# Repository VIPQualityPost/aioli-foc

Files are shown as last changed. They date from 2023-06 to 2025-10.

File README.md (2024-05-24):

# AIOLI-FOC (All In One Low I - FOC)

Small, low current (I) closed loop simpleFOC driver board, that can be assembled for &lt;$10 with mostly basic components at LCSC. Has USB C for power, serial communication (USB CDC), and DFU firmware updates. The CANBUS peripheral is exposed on both edges for "stitching" boards together using the Kyocera B2B connector used on the STLINK-V3-MINIE. SWD + UART via STLINK 14 pin connector.

The target for this project was to create an all-in-one simpleFOC board with high resolution magnetic encoder, better MCU than the previous STM32F103, CANBUS for multi board communication, and be assembled with top-side only components. The board is 4 layers (which at this size, does not add any cost over the 2-layers). Additionally, it has a compact size of 40x40mm.

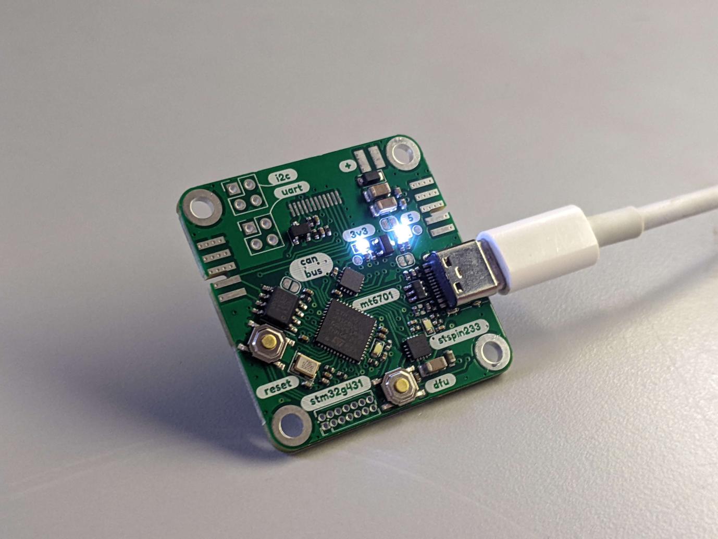
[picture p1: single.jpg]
Photo of PCB

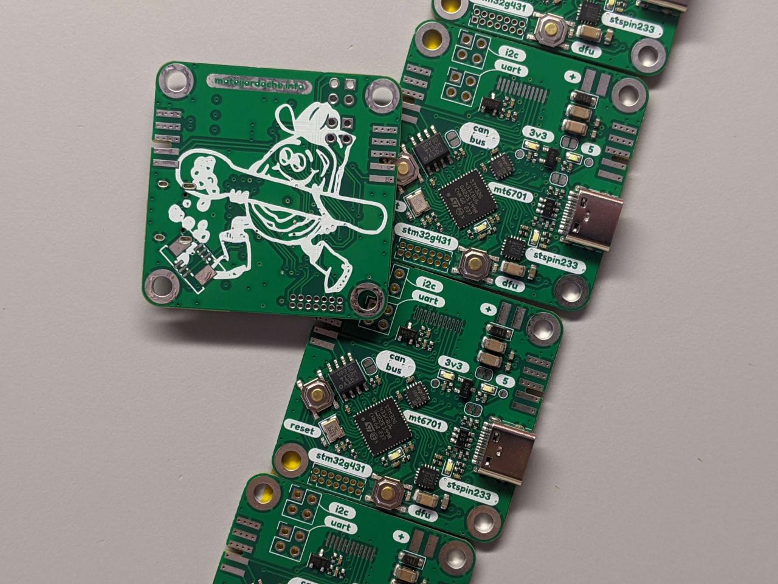
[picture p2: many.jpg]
Photo of PCBs


# Building

- Install [platformio core](https://docs.platformio.org/en/latest/core/installation/methods/index.html)
- Run `pio run`

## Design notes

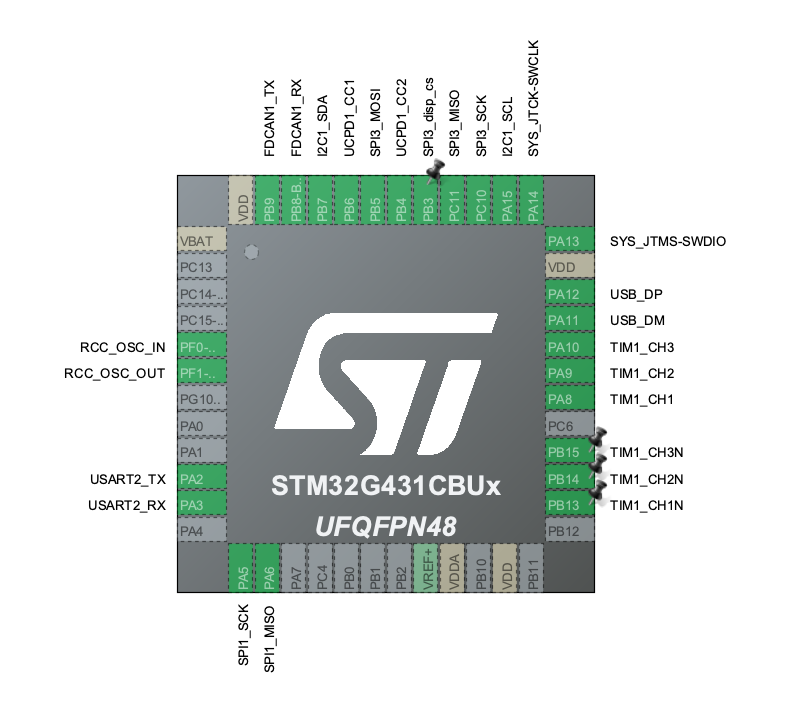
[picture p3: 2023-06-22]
stm32g431-pinout.png

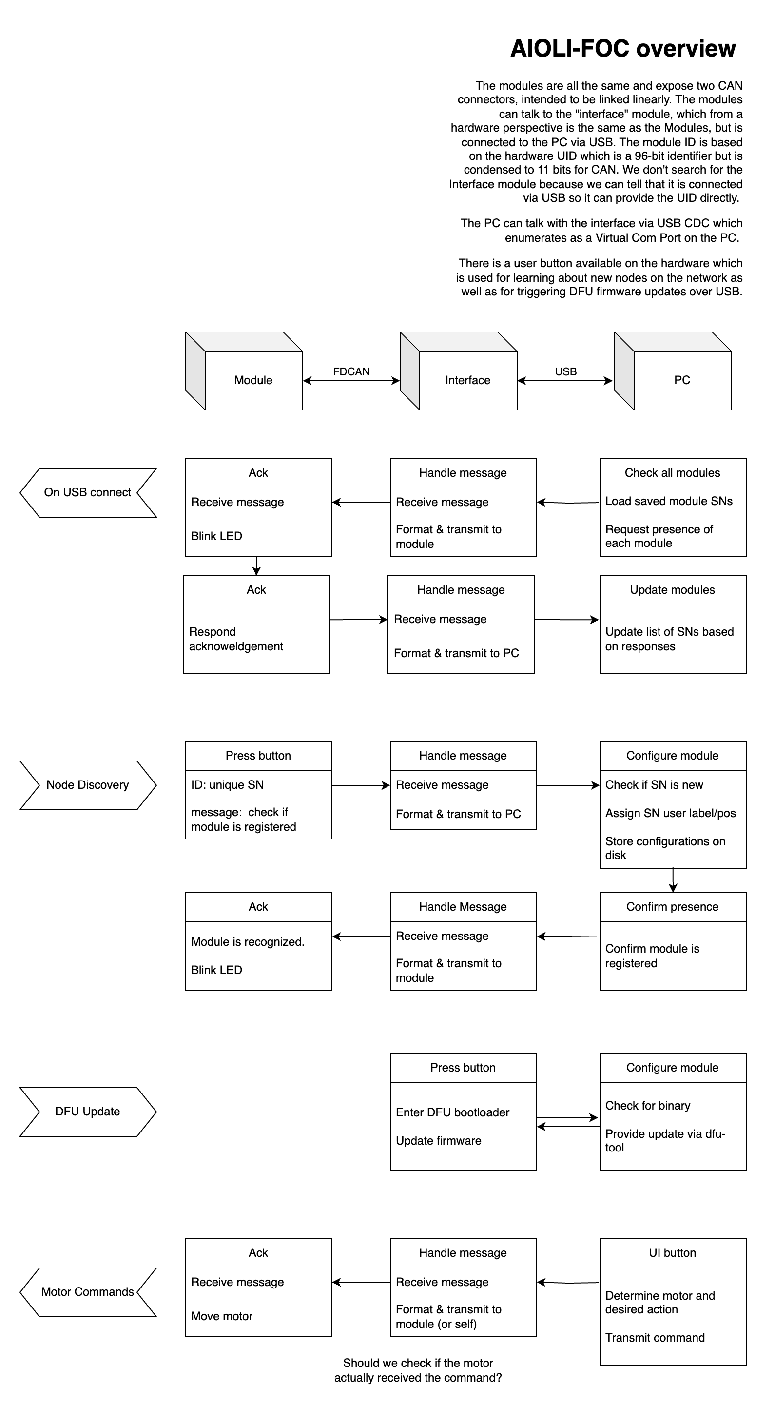
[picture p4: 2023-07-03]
aioli-foc-overview.png

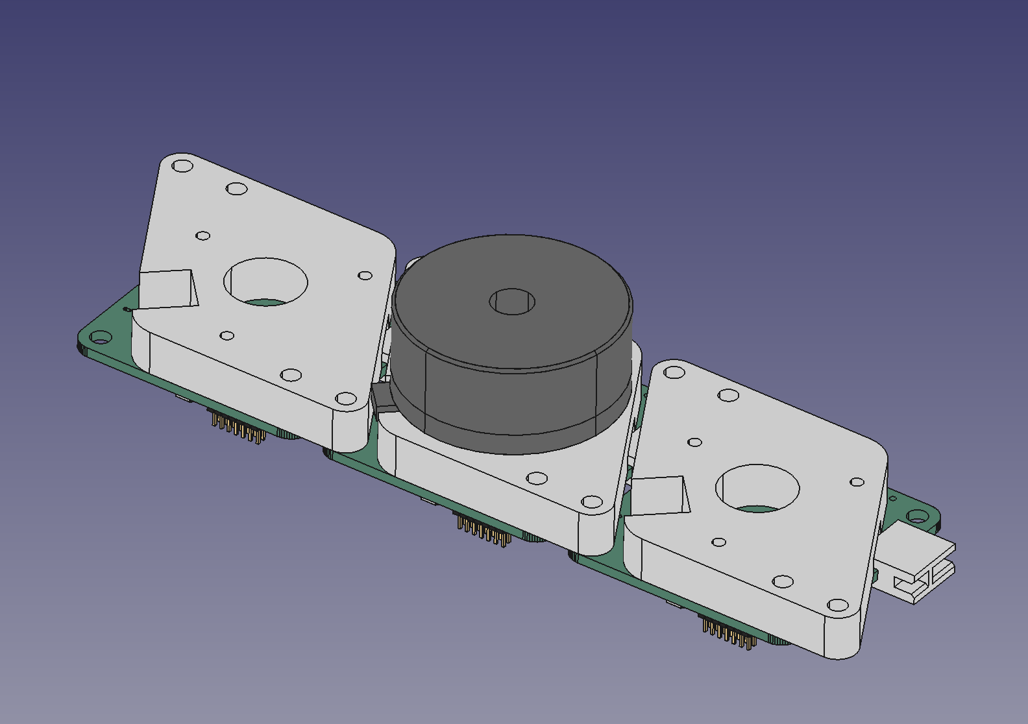
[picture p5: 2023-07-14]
mechanical/motor_MAD/render.png

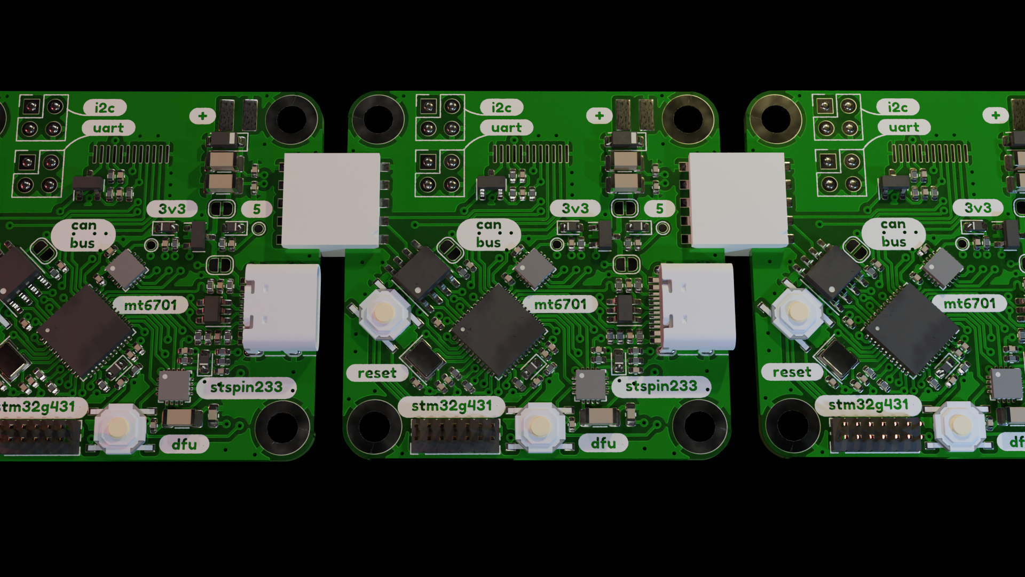
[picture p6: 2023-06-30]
render.png

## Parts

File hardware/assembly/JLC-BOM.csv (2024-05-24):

Comment | Designator | Footprint | JLCPCB Part #
USB_C_Receptacle_USB2.0 | J601 | HRO_TYPE-C-31-M-12 | C165948
10u | C707,C705 | 0402_C
SN65HVD230 | U101 | SOIC-8 | C12084
22R | R206,R207,R502 | 0402_R
3.3k | R303,R702 | 0402_R
0.1u | C502,C501,C202,C204,C101,C401,C203,C201,C207,C208 | 0402_C
18k | R301,R302 | 0402_R
AO3400A | Q501 | SOT-23 | C20917
10k | R203,R401,R501,R202,R503 | 0402_R
22u | C303 | 0603_C
10n | C302 | 0402_C
1u | C706,C702 | 0402_C
LED | D301,D201,D701,D702 | 0603_D | C2290
100u | C701,C704,C703 | 1206_C
20p | C205,C206 | 0402_C
B5819W | D101 | D_SOD-123 | C8598
12MHz | Y201 | Crystal_3225 | C9002
SRV05-4 | U601 | SOT-23-6 | C85364
STSPIN233 | U301 | VQFN-16 | C2653468
5.1k | R204,R701,R201,R205 | 0402_R
XC6206 | U701 | SOT-23 | C5446
47p | C602,C601 | 0402_C
STM32G431 | U201 | QFN-48 | C529356
2.2u | C304 | 0402_C
120R | R101 | 0402_R
BUTTON | SW201,SW202 | TS-1187A-B-A-B | C318884
1n | C301 | 0402_C
MT6701 | U401 | QFN-16 | C2913974

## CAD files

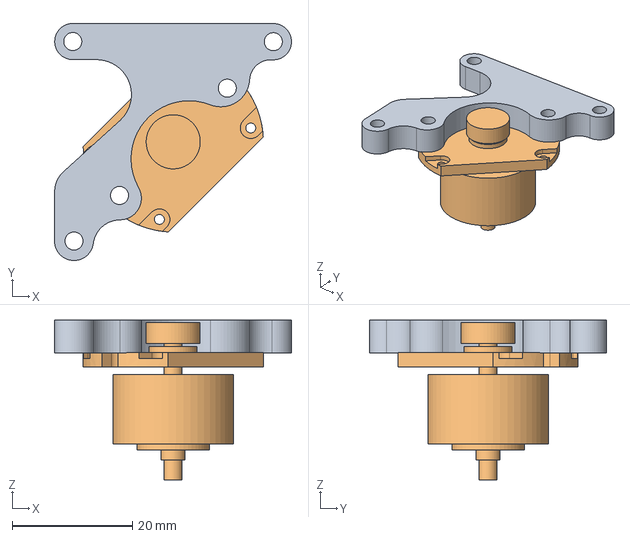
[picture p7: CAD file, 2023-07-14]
mechanical/motor_FPC/aiolifoc.FCStd
39.4 x 39.4 x 26.6 mm
mountingplate

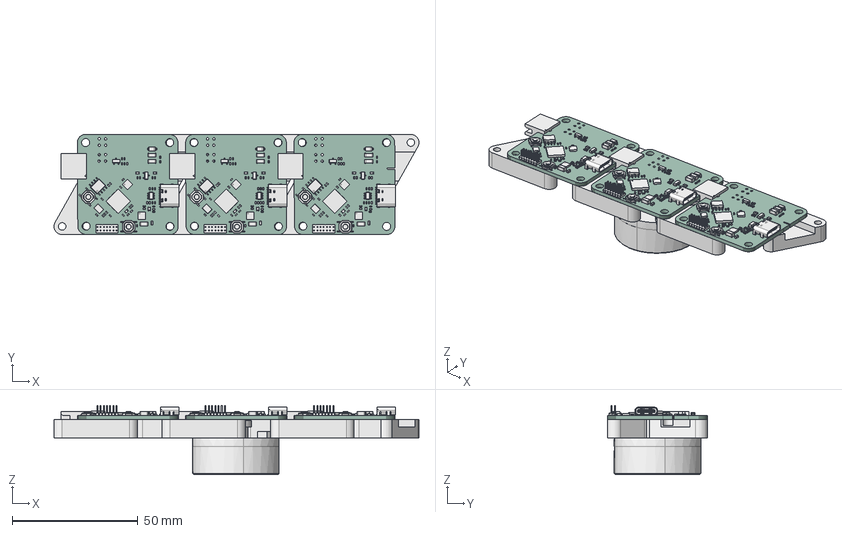
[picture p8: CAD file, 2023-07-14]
mechanical/motor_MAD/aiolifoc-backplane.FCStd
144.8 x 39.8 x 27.5 mm
stm32g431-mt6701-stspin233 PCB
stm32g431-mt6701-stspin233 PCB001
stm32g431-mt6701-stspin233 PCB002
Product

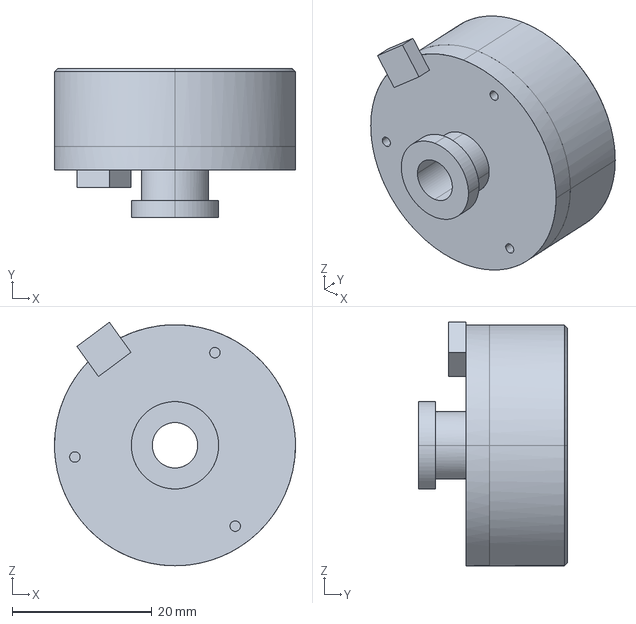
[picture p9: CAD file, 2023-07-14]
mechanical/motor_MAD/mad2408.step
34.5 x 21.4 x 34.9 mm

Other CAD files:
mechanical/motor_FPC/aiolifoc.stl
mechanical/motor_MAD/aiolifoc-backplane.stl
mechanical/motor_MAD/mad2408.stl

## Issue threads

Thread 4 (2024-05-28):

V2 To Do List Brainstorming

vitaminmoo, 2024-05-28:
Just brainstorming some notes on changes I think would be good for the next rev

- Make it square, including the mounting holes
- Move the stm32g431 connector away from the mounting screw so the stlink cable doesn't interfere
- Put an upward-firing neopixel or other RGB LED pad directly in the center on the flat side for the ability to light pipe up the motor shaft tube - Thickness might be an issue with magnet spacing though

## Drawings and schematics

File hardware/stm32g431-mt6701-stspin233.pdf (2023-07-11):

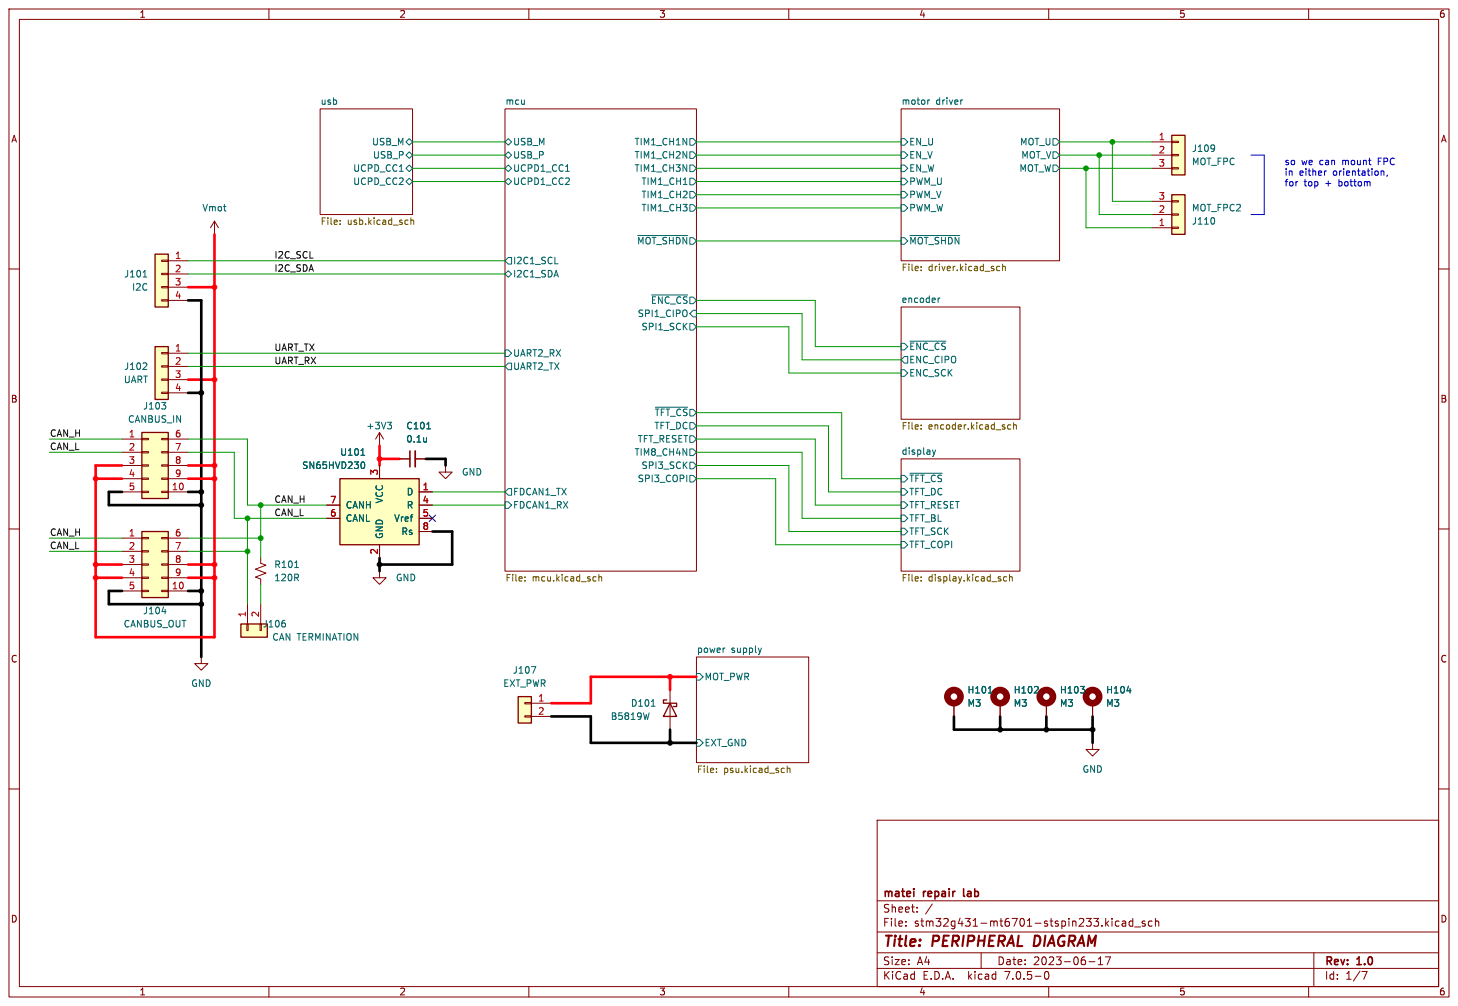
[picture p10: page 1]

so we can mount FPC
in either orientation,
for top + bottom

power supply File: psu.kicad_sch

File: stm32g431-mt6701-stspin233.kicad_sch Sheet: / matei repair lab

Id: 1/7 Title: PERIPHERAL DIAGRAM

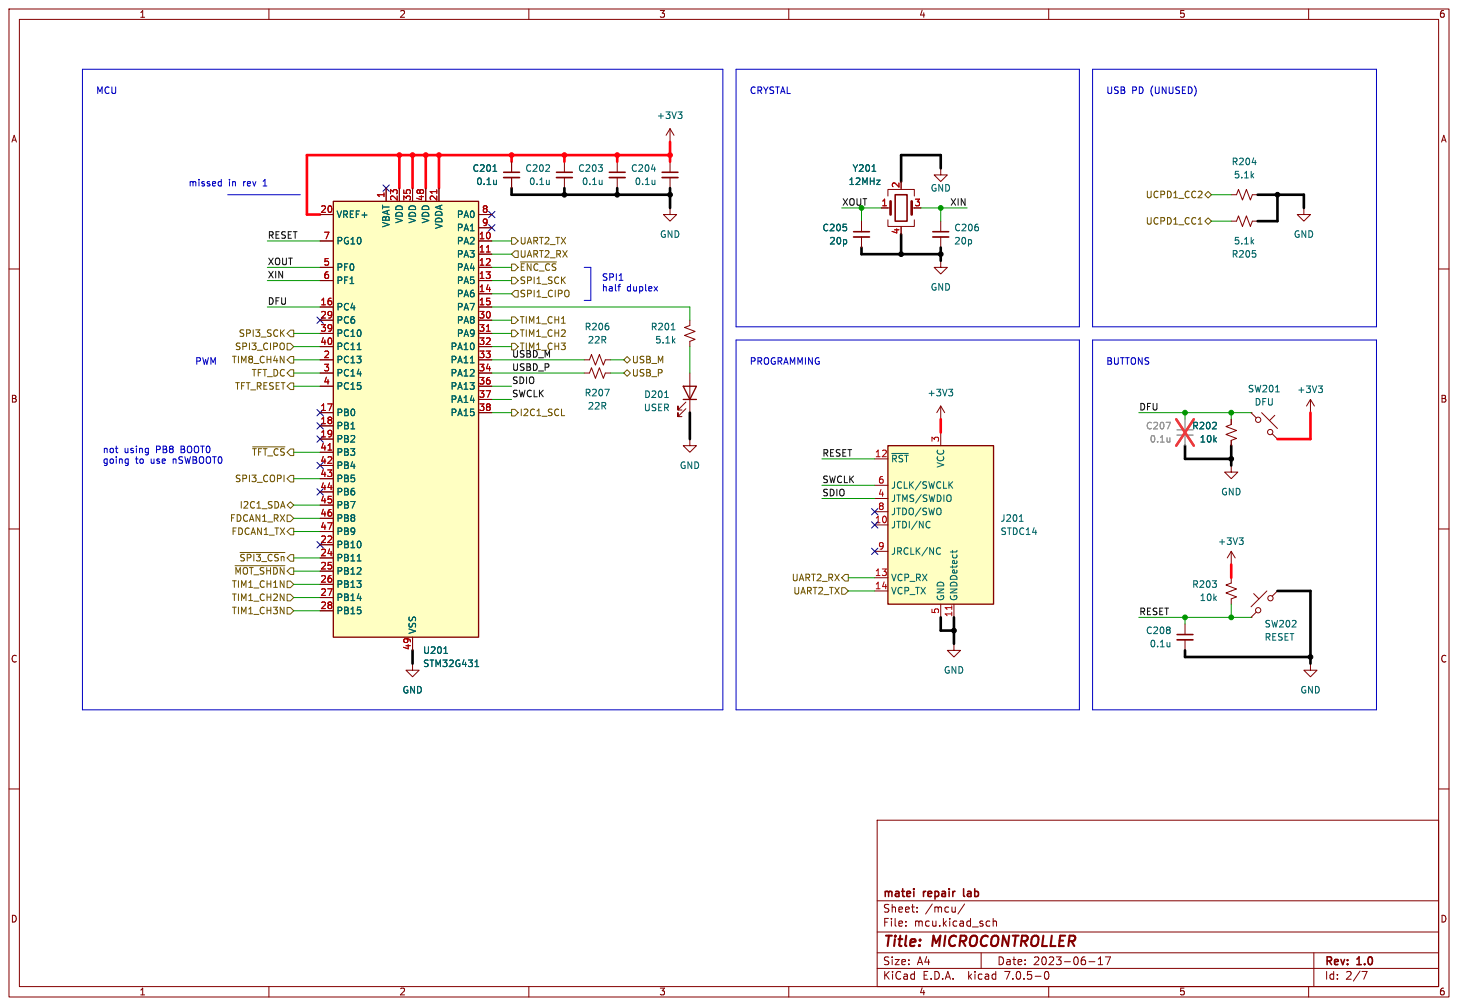
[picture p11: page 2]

going to use nSWBOOT0 MCU
0.1u U201 STM32G431 VBAT
22R GND VBAT

1 PA2 10 PA3 11 PA4 12 PA5 13 PA6 14 PA7 15 PC4 16 PB0 17 PB1 18 PB2 19 PC13 2 VREF+ 20 VDDA 21 PB10 22 VDD 23 PB11 24 PB12 25 PB13 26 PB14 27 PB15 28 PC6 29 PC14 3 PA8 30 PA9 31 PA10 32 PA11 33 PA12 34 VDD 35 PA13 36 PA14 37 PA15 38 PC10 39 PC15 4 PC11 40 PB3 41 PB4 42 PB5 43 PB6 44 PB7 45 PB8 46 PB9 47 VDD 48 VSS 49 PF0 5 PF1 6 PG10 7 PA0 8 PA1 9 U201 STM32G431

1 PA2 10 PA3 11 PA4 12 PA5 13 PA6 14 PA7 15 PC4 16 PB0 17 PB1 18 PB2 19 PC13 2 VREF+ 20 VDDA 21 PB10 22 VDD 23 PB11 24 PB12 25 PB13 26 PB14 27 PB15 28 PC6 29 PC14 3 PA8 30 PA9 31 PA10 32 PA11 33 PA12 34 VDD 35 PA13 36 PA14 37 PA15 38 PC10 39 PC15 4 PC11 40 PB3 41 PB4 42 PB5 43 PB6 44 PB7 45 PB8 46 PB9 47 VDD 48 VSS 49 PF0 5 PF1 6 PG10 7 PA0 8 PA1 9 GND

File: mcu.kicad_sch Sheet: /mcu/ matei repair lab

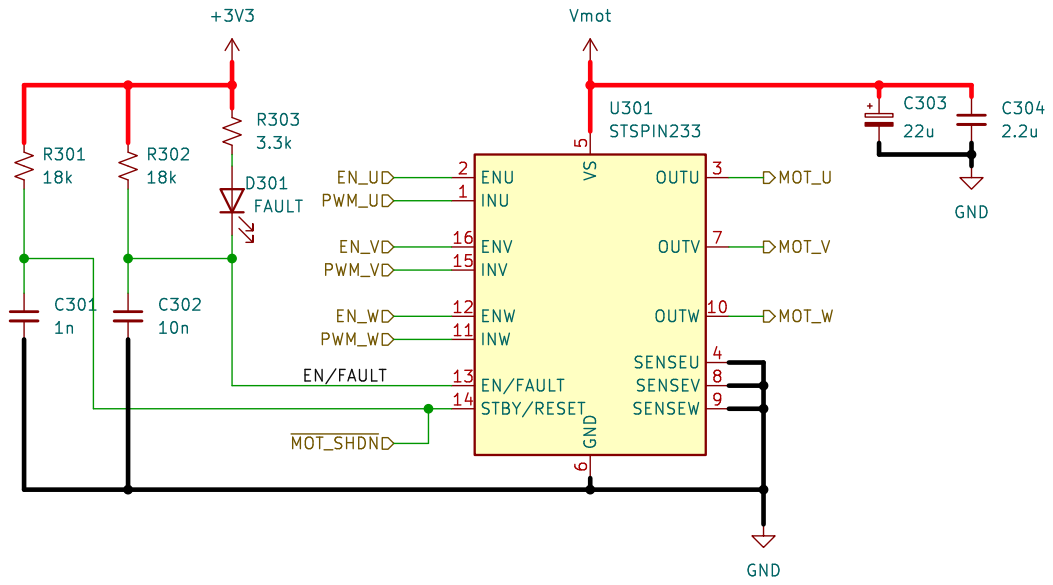
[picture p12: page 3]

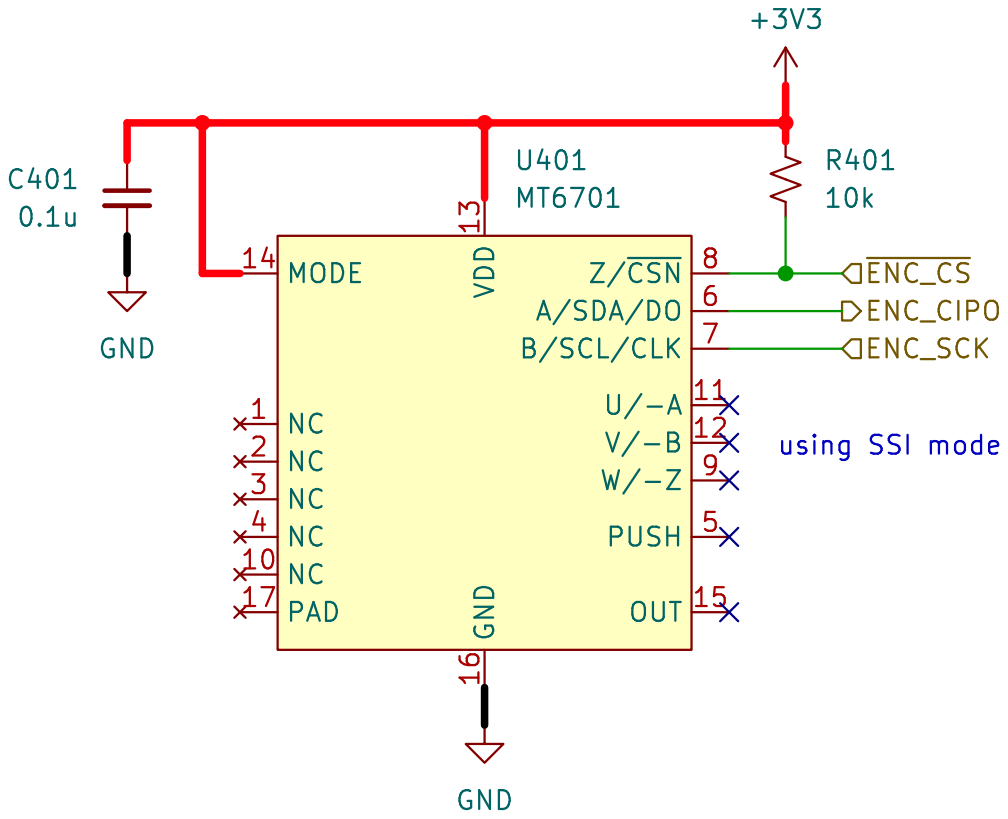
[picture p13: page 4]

File: encoder.kicad_sch Sheet: /encoder/ matei repair lab GND

Id: 4/7 Title: MAGNETIC ENCODER 14 BIT

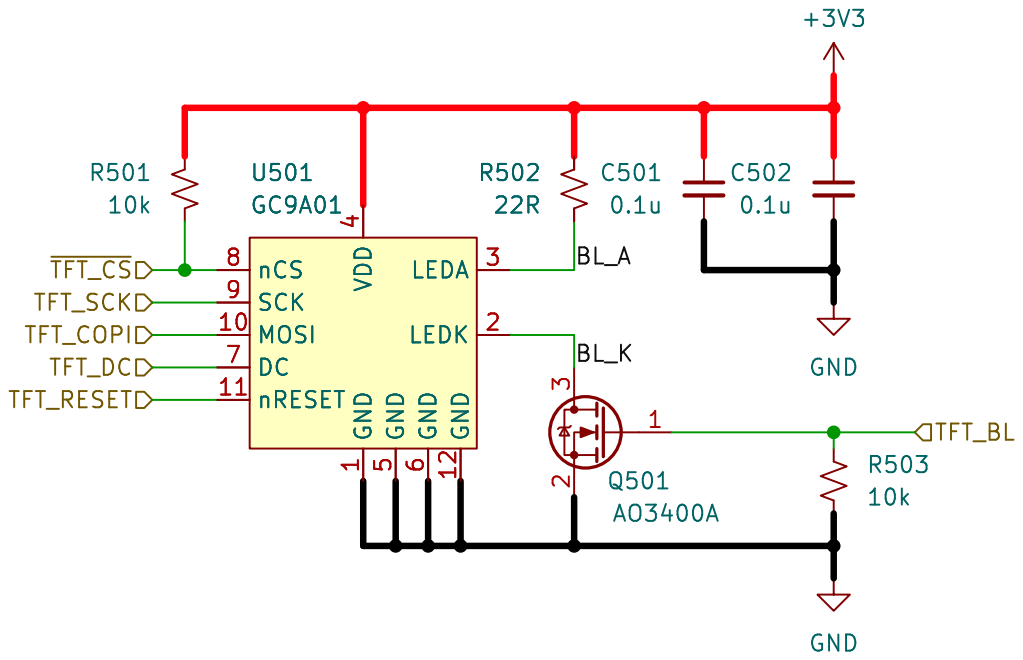
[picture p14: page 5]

File: display.kicad_sch Sheet: /display/ matei repair lab

Id: 5/7 Title: GC9A01 TFT DISPLAY

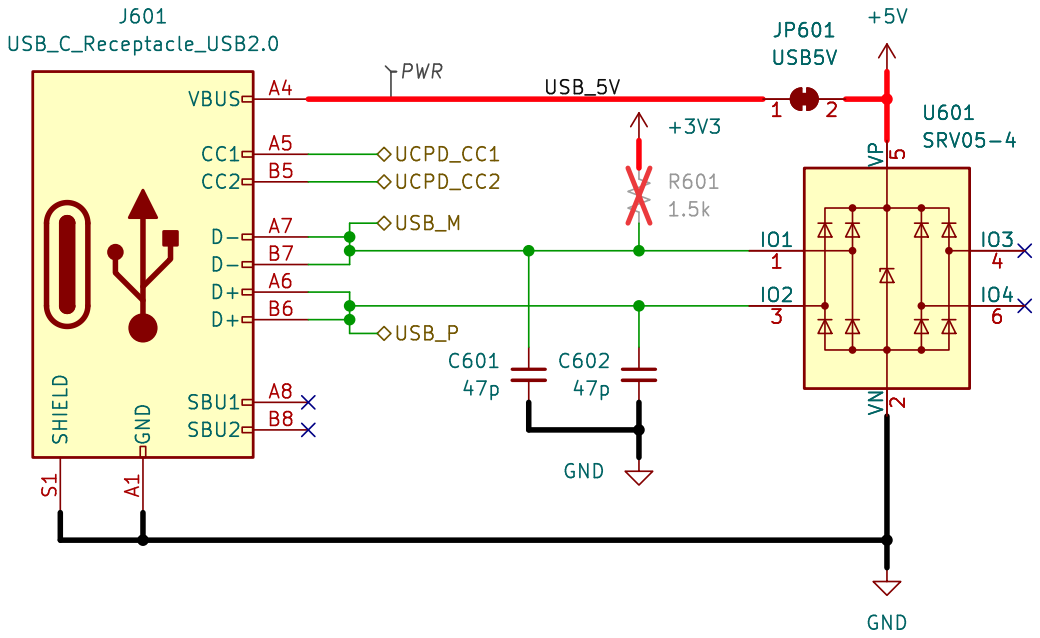
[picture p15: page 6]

File: usb.kicad_sch Sheet: /usb/ matei repair lab GND GND

Id: 6/7 Title: USB & ESD

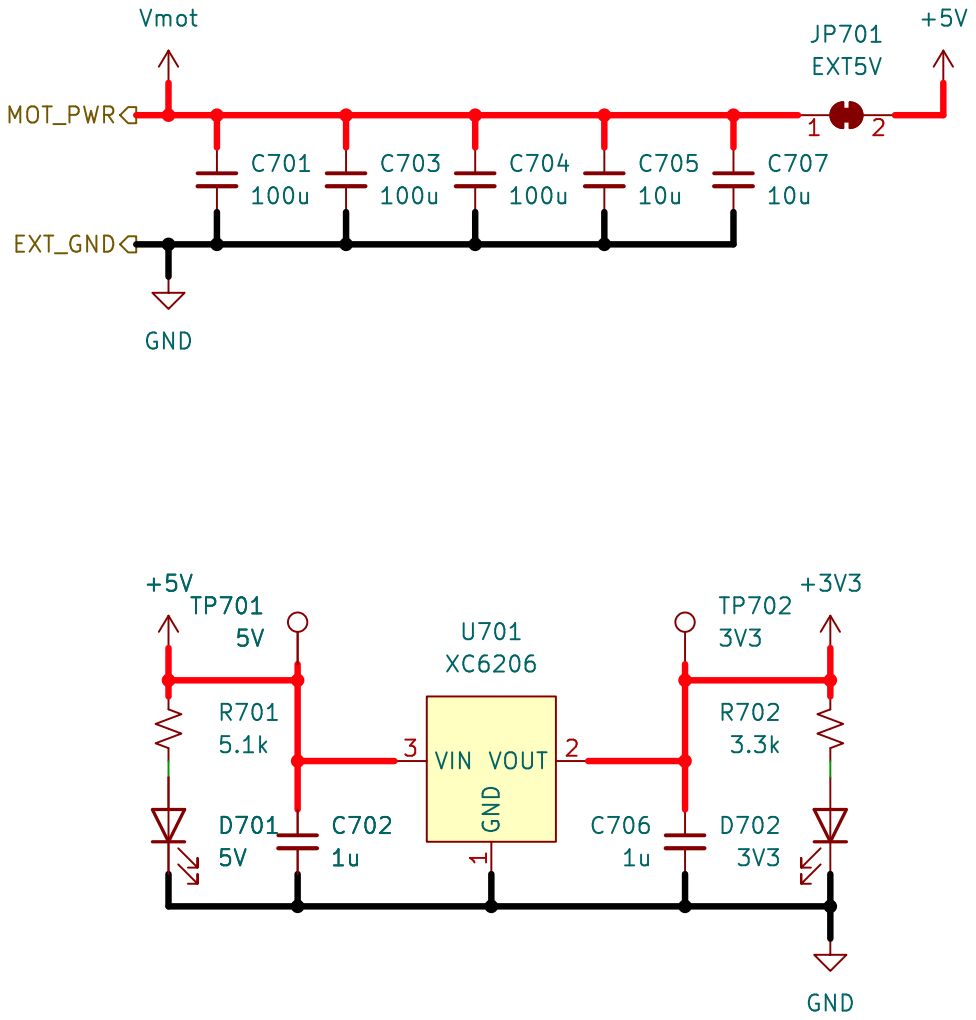
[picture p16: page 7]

Id: 7/7 Title: POWER SUPPLY & FILTERING

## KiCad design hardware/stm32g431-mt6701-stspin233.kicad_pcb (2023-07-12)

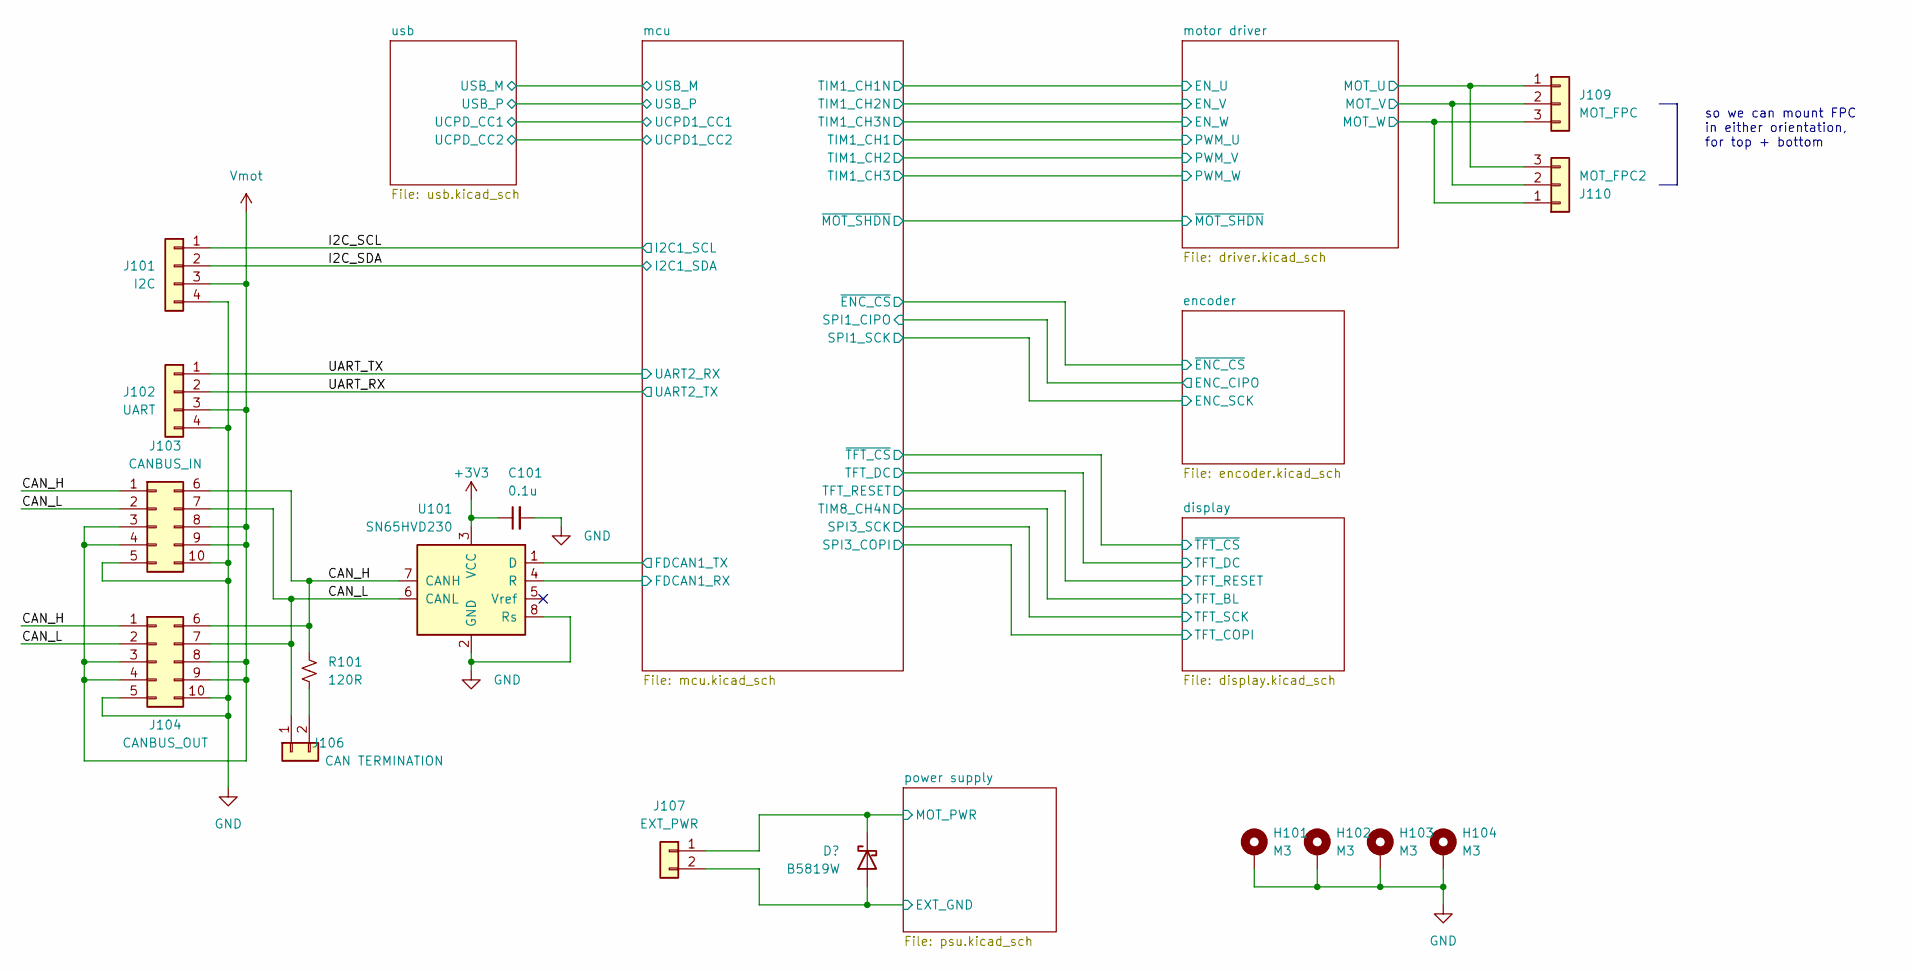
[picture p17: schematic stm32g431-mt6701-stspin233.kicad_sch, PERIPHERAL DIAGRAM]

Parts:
C101: 0.1u; C_0402_1005Metric
D101: B5819W; D_SOD-123
H101, H102, H103, H104: M3; MountingHole_3.2mm_M3_DIN965_Pad
J101: I2C; PinHeader_2x02_P2.54mm_Vertical
J102: UART; PinHeader_2x02_P2.54mm_Vertical
J103: CANBUS_IN; AVX-009159010061911
J104: CANBUS_OUT; AVX-009159010061911
J106: CAN TERMINATION; SolderJumper-2_P1.3mm_Open_RoundedPad1.0x1.5mm
J107: EXT_PWR; JST-XH-edgemount-2p
J109: MOT_FPC; FPC-SMD_3P-P1.00_HDGC_1.0K-LS-3PWB-BOTTOMCONTACT
J110: MOT_FPC2; FPC-SMD_3P-P1.00_HDGC_1.0K-LS-3PWB-BOTTOMCONTACT
R101: 120R; R_0402_1005Metric
U101: SN65HVD230; SOIC-8_3.9x4.9mm_P1.27mm

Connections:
+3V3: C101.1, U101.3 (VCC); also elsewhere on the board
/CAN_H: J103.1, J103.6, J104.1, J104.6, R101.2, U101.7 (CANH)
/CAN_L: J103.2, J103.7, J104.2, J104.7, J106.1, U101.6 (CANL)
/I2C_SCL: J101.1; also elsewhere on the board
/I2C_SDA: J101.2; also elsewhere on the board
/UART_RX: J102.2; also elsewhere on the board
/UART_TX: J102.1; also elsewhere on the board
/mcu/FDCAN1_RX: U101.4 (R); also elsewhere on the board
/mcu/FDCAN1_TX: U101.1 (D); also elsewhere on the board
/motor driver/MOT_U: J109.1, J110.3; also elsewhere on the board
/motor driver/MOT_V: J109.2, J110.2; also elsewhere on the board
/motor driver/MOT_W: J109.3, J110.1; also elsewhere on the board
GND: C101.2, D101.2 (A), H101.1, H102.1, H103.1, H104.1, J101.4, J102.4, J103.5, J103.10, J104.5, J104.10, J107.2, U101.2 (GND), U101.8 (Rs); also elsewhere on the board
unnamed: J106.2, R101.1
Vmot: D101.1 (K), J101.3, J102.3, J103.3, J103.4, J103.8, J103.9, J104.3, J104.4, J104.8, J104.9, J107.1; also elsewhere on the board

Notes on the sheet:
so we can mount FPC in either orientation, for top + bottom

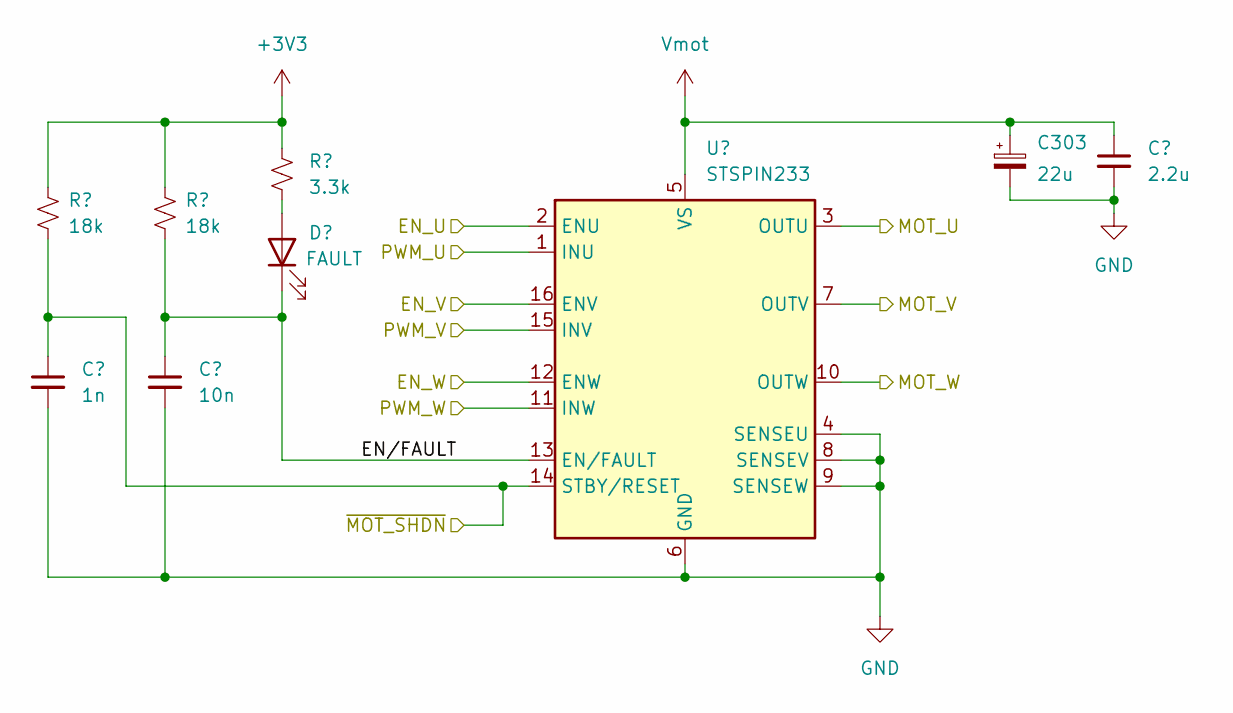
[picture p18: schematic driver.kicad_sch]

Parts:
C301: 1n; C_0402_1005Metric
C302: 10n; C_0402_1005Metric
C303: 22u; C_0603_1608Metric
C304: 2.2u; C_0402_1005Metric
D301: FAULT; D_0603_1608Metric
R301, R302: 18k; R_0402_1005Metric
R303: 3.3k; R_0402_1005Metric
U301: STSPIN233; VQFN-16-1EP_3x3mm_P0.5mm_EP1.8x1.8mm

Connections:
+3V3: R301.1, R302.1, R303.2; also elsewhere on the board
/mcu/TIM1_CH1: U301.1 (INU); also elsewhere on the board
/mcu/TIM1_CH1N: U301.2 (ENU); also elsewhere on the board
/mcu/TIM1_CH2: U301.15 (INV); also elsewhere on the board
/mcu/TIM1_CH2N: U301.16 (ENV); also elsewhere on the board
/mcu/TIM1_CH3: U301.11 (INW); also elsewhere on the board
/mcu/TIM1_CH3N: U301.12 (ENW); also elsewhere on the board
/mcu/~MOT_SHDN: C301.1, R301.2, U301.14 (STBY/RESET); also elsewhere on the board
/motor driver/EN/FAULT: C302.1, D301.1 (K), R302.2, U301.13 (EN/FAULT)
/motor driver/MOT_U: U301.3 (OUTU); also elsewhere on the board
/motor driver/MOT_V: U301.7 (OUTV); also elsewhere on the board
/motor driver/MOT_W: U301.10 (OUTW); also elsewhere on the board
GND: C301.2, C302.2, C303.2, C304.2, U301.4 (SENSEU), U301.6 (GND), U301.8 (SENSEV), U301.9 (SENSEW), U301.17 (GND); also elsewhere on the board
unnamed: D301.2 (A), R303.1
Vmot: C303.1, C304.1, U301.5 (VS); also elsewhere on the board

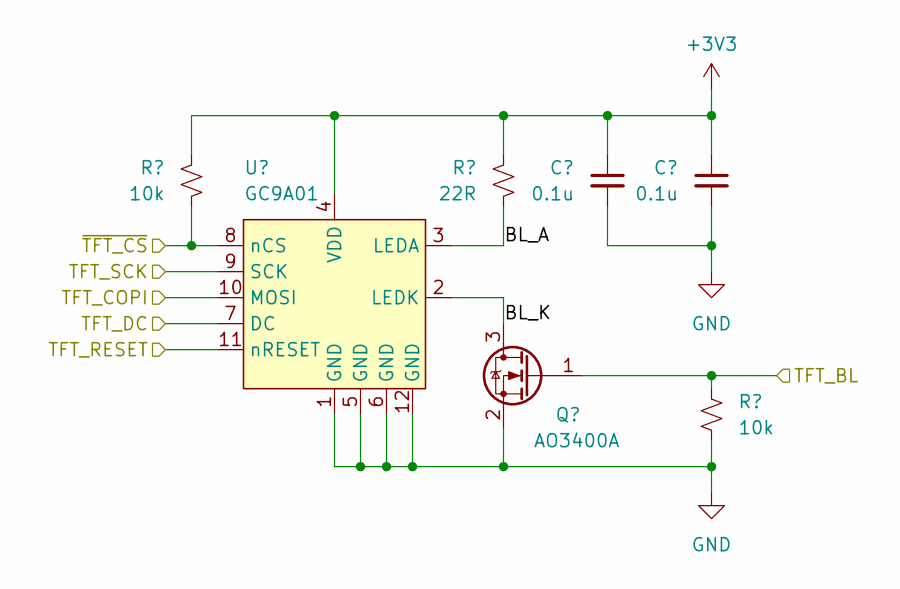
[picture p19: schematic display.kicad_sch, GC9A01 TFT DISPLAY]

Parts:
C501, C502: 0.1u; C_0402_1005Metric
Q501: AO3400A; SOT-23
R501, R503: 10k; R_0402_1005Metric
R502: 22R; R_0402_1005Metric
U501: GC9A01; GC9A01Round1.28_flipped_mount_easy_esc

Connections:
+3V3: C501.1, C502.1, R501.1, R502.1, U501.4 (VDD); also elsewhere on the board
/display/BL_A: R502.2, U501.3 (LEDA)
/display/BL_K: Q501.3 (D), U501.2 (LEDK)
/display/TFT_BL: Q501.1 (G), R503.1; also elsewhere on the board
/display/TFT_COPI: U501.10 (MOSI); also elsewhere on the board
/display/TFT_DC: U501.7 (DC); also elsewhere on the board
/display/TFT_RESET: U501.11 (nRESET); also elsewhere on the board
/display/TFT_SCK: U501.9 (SCK); also elsewhere on the board
/display/~TFT_CS: R501.2, U501.8 (nCS); also elsewhere on the board
GND: C501.2, C502.2, Q501.2 (S), R503.2, U501.1 (GND), U501.5 (GND), U501.6 (GND), U501.12 (GND); also elsewhere on the board

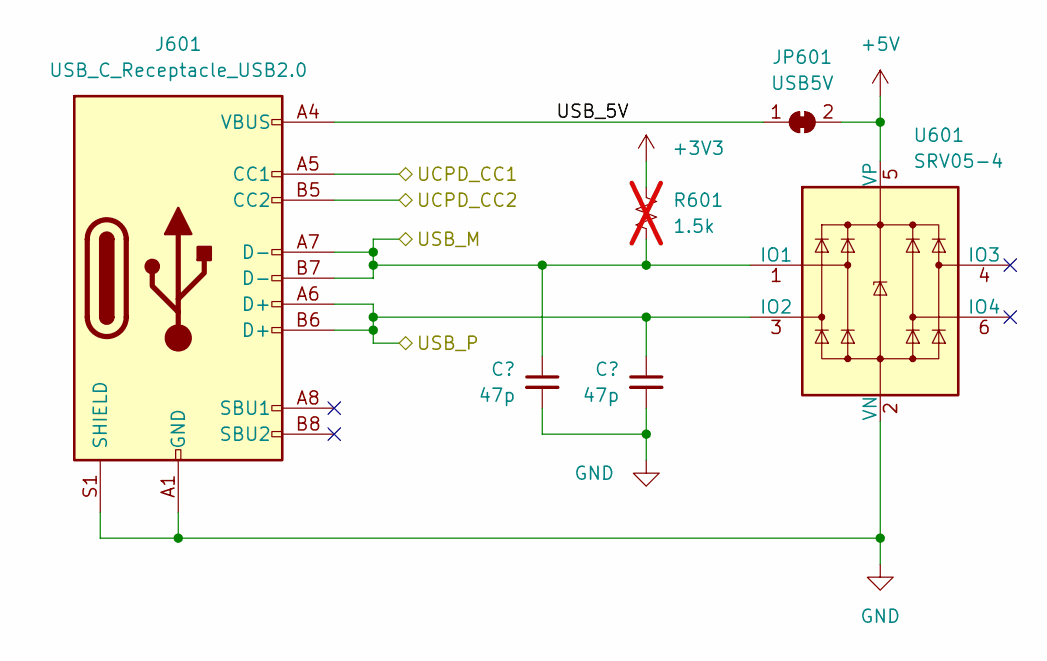
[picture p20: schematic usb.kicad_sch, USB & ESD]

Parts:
C601, C602: 47p; C_0402_1005Metric
J601: USB_C_Receptacle_USB2.0; USB_C_Receptacle_HRO_TYPE-C-31-M-12
JP601: USB5V; SolderJumper-2_P1.3mm_Bridged_RoundedPad1.0x1.5mm
R601: 1.5k; R_0402_1005Metric; not fitted
U601: SRV05-4; SOT-23-6

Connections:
+3V3: R601.1; also elsewhere on the board
+5V: JP601.2 (B), U601.5 (VP); also elsewhere on the board
/mcu/UCPD1_CC1: J601.A5 (CC1); also elsewhere on the board
/mcu/UCPD1_CC2: J601.B5 (CC2); also elsewhere on the board
/mcu/USB_M: C601.1, J601.A7 (D-), J601.B7 (D-), R601.2, U601.1 (IO1); also elsewhere on the board
/mcu/USB_P: C602.1, J601.A6 (D+), J601.B6 (D+), U601.3 (IO2); also elsewhere on the board
/usb/USB_5V: J601.A4 (VBUS), J601.A9 (VBUS), J601.B4 (VBUS), J601.B9 (VBUS), JP601.1 (A)
GND: C601.2, C602.2, J601.A1 (GND), J601.A12 (GND), J601.B1 (GND), J601.B12 (GND), J601.S1 (SHIELD), U601.2 (VN); also elsewhere on the board

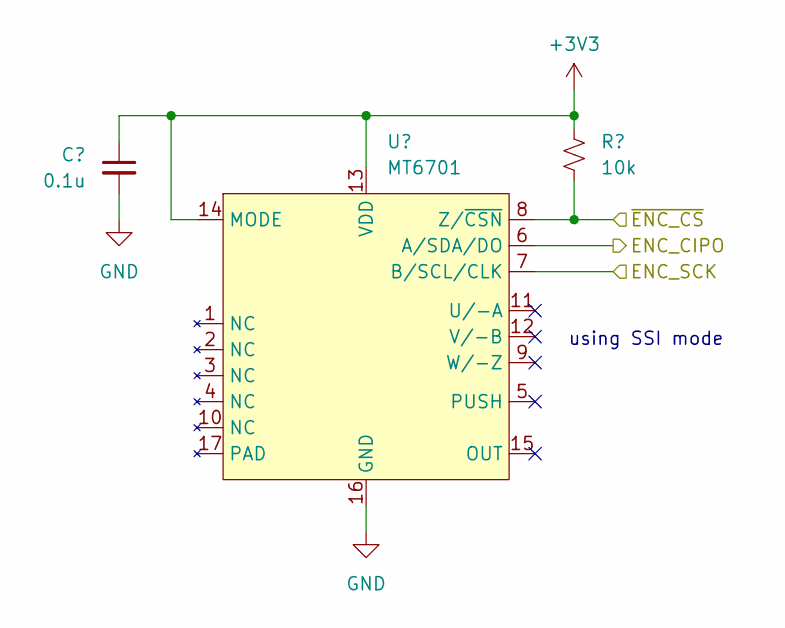
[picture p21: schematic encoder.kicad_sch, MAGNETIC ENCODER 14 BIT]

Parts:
C401: 0.1u; C_0402_1005Metric
R401: 10k; R_0402_1005Metric
U401: MT6701; QFN-16-1EP_3x3mm_P0.5mm_EP1.7x1.7mm

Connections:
+3V3: C401.1, R401.1, U401.13 (VDD), U401.14 (MODE); also elsewhere on the board
/encoder/ENC_CIPO: U401.6 (A/SDA/DO); also elsewhere on the board
/encoder/ENC_SCK: U401.7 (B/SCL/CLK); also elsewhere on the board
/encoder/~ENC_CS: R401.2, U401.8 (Z/~CSN); also elsewhere on the board
GND: C401.2, U401.16 (GND); also elsewhere on the board

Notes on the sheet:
using SSI mode

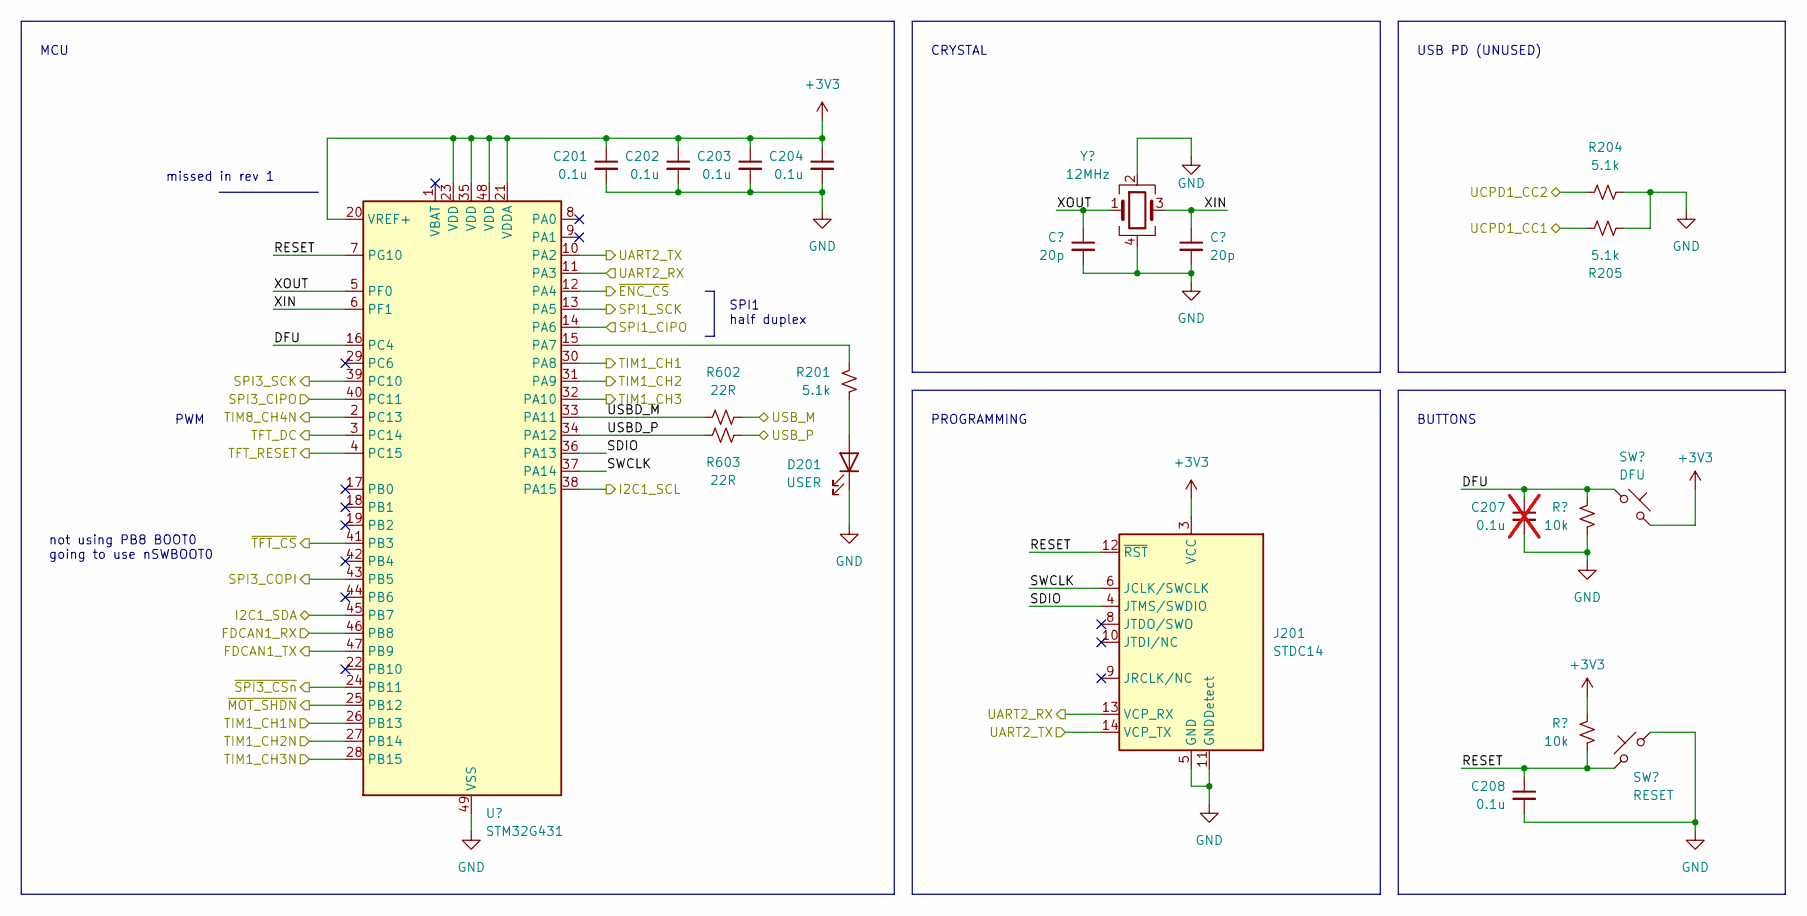
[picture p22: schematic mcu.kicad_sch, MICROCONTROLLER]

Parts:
C201, C202, C203, C204, C208: 0.1u; C_0402_1005Metric
C205, C206: 20p; C_0402_1005Metric
C207: 0.1u; C_0402_1005Metric; not fitted
D201: USER; D_0603_1608Metric
J201: STDC14; PinHeader_2x07_P1.27mm_Vertical
R201, R204, R205: 5.1k; R_0402_1005Metric
R202, R203: 10k; R_0402_1005Metric
R602, R603: 22R; R_0402_1005Metric
SW201: DFU; TS-1187A-B-A-B
SW202: RESET; TS-1187A-B-A-B
U201: STM32G431; QFN-48-1EP_7x7mm_P0.5mm_EP5.6x5.6mm
Y201: 12MHz; Crystal_SMD_3225-4Pin_3.2x2.5mm

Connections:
+3V3: C201.1, C202.1, C203.1, C204.1, J201.3 (VCC), R203.1, SW201.2, U201.20 (VREF+), U201.21 (VDDA), U201.23 (VDD), U201.35 (VDD), U201.48 (VDD); also elsewhere on the board
/I2C_SCL: U201.38 (PA15); also elsewhere on the board
/I2C_SDA: U201.45 (PB7); also elsewhere on the board
/UART_RX: J201.14 (VCP_TX), U201.10 (PA2); also elsewhere on the board
/UART_TX: J201.13 (VCP_RX), U201.11 (PA3); also elsewhere on the board
/display/TFT_BL: U201.2 (PC13); also elsewhere on the board
/display/TFT_COPI: U201.43 (PB5); also elsewhere on the board
/display/TFT_DC: U201.3 (PC14); also elsewhere on the board
/display/TFT_RESET: U201.4 (PC15); also elsewhere on the board
/display/TFT_SCK: U201.39 (PC10); also elsewhere on the board
/display/~TFT_CS: U201.41 (PB3); also elsewhere on the board
/encoder/ENC_CIPO: U201.14 (PA6); also elsewhere on the board
/encoder/ENC_SCK: U201.13 (PA5); also elsewhere on the board
/encoder/~ENC_CS: U201.12 (PA4); also elsewhere on the board
/mcu/DFU: C207.1, R202.1, SW201.1, U201.16 (PC4)
/mcu/FDCAN1_RX: U201.46 (PB8); also elsewhere on the board
/mcu/FDCAN1_TX: U201.47 (PB9); also elsewhere on the board
/mcu/RESET: C208.1, J201.12 (~RST), R203.2, SW202.1, U201.7 (PG10)
/mcu/SDIO: J201.4 (JTMS/SWDIO), U201.36 (PA13)
/mcu/SPI3_CIPO: U201.40 (PC11)
/mcu/SWCLK: J201.6 (JCLK/SWCLK), U201.37 (PA14)
/mcu/TIM1_CH1: U201.30 (PA8); also elsewhere on the board
/mcu/TIM1_CH1N: U201.26 (PB13); also elsewhere on the board
/mcu/TIM1_CH2: U201.31 (PA9); also elsewhere on the board
/mcu/TIM1_CH2N: U201.27 (PB14); also elsewhere on the board
/mcu/TIM1_CH3: U201.32 (PA10); also elsewhere on the board
/mcu/TIM1_CH3N: U201.28 (PB15); also elsewhere on the board
/mcu/UCPD1_CC1: R205.2; also elsewhere on the board
/mcu/UCPD1_CC2: R204.1; also elsewhere on the board
/mcu/USBD_M: U201.33 (PA11); also elsewhere on the board
/mcu/USBD_P: U201.34 (PA12); also elsewhere on the board
/mcu/XIN: C206.1, U201.6 (PF1), Y201.3
/mcu/XOUT: C205.1, U201.5 (PF0), Y201.1
/mcu/~MOT_SHDN: U201.25 (PB12); also elsewhere on the board
/mcu/~SPI3_CSn: U201.24 (PB11)
GND: C201.2, C202.2, C203.2, C204.2, C205.2, C206.2, C207.2, C208.2, D201.1 (K), J201.5 (GND), J201.7 (GND), J201.11 (GNDDetect), R202.2, R204.2, R205.1, SW202.2, U201.49 (VSS), Y201.2, Y201.4; also elsewhere on the board
unnamed: D201.2 (A), R201.2
unnamed: R201.1, U201.15 (PA7)

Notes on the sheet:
PROGRAMMING
BUTTONS
not using PB8 BOOT0 going to use nSWBOOT0
MCU
missed in rev 1
PWM
CRYSTAL
USB PD (UNUSED)
SPI1 half duplex

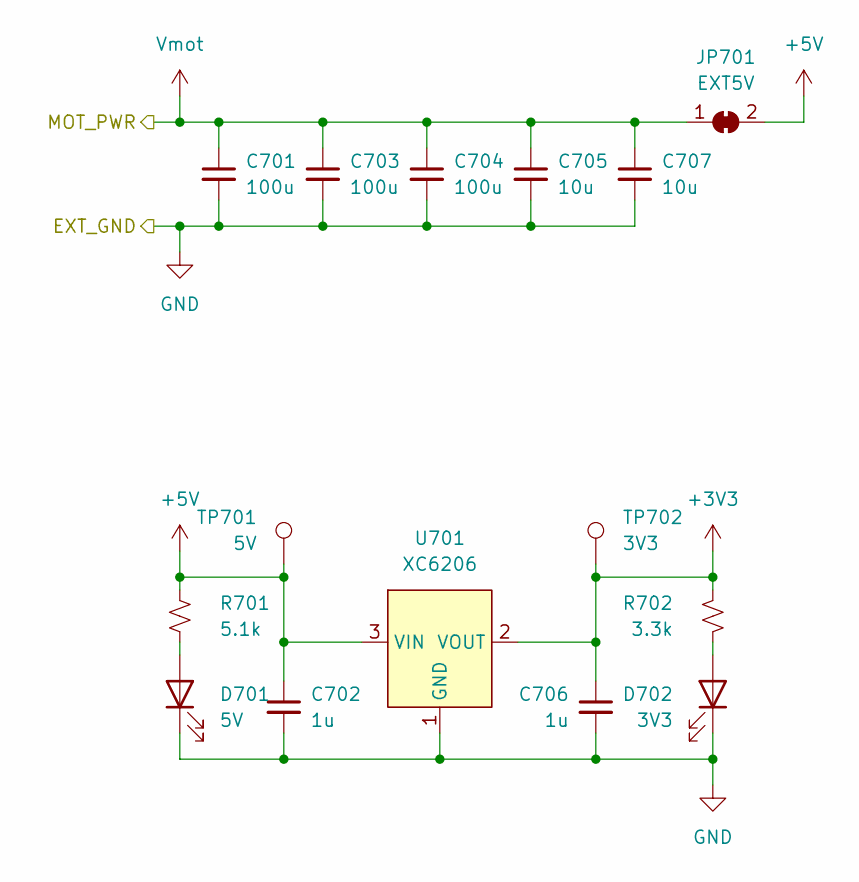
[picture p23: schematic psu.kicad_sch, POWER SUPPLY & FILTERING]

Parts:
C701, C703, C704: 100u; C_1206_3216Metric
C702, C706: 1u; C_0402_1005Metric
C705, C707: 10u; C_0402_1005Metric
D701: 5V; D_0603_1608Metric
D702: 3V3; D_0603_1608Metric
JP701: EXT5V; SolderJumper-2_P1.3mm_Bridged_RoundedPad1.0x1.5mm
R701: 5.1k; R_0402_1005Metric
R702: 3.3k; R_0402_1005Metric
TP701: 5V; TestPoint_Pad_D1.0mm
TP702: 3V3; TestPoint_Pad_D1.0mm
U701: XC6206; SOT-23

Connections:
+3V3: C706.1, R702.1, TP702.1, U701.2 (VOUT); also elsewhere on the board
+5V: C702.1, JP701.2 (B), R701.1, TP701.1, U701.3 (VIN); also elsewhere on the board
GND: C701.2, C702.2, C703.2, C704.2, C705.2, C706.2, C707.2, D701.1 (K), D702.1 (K), U701.1 (GND); also elsewhere on the board
unnamed: D701.2 (A), R701.2
unnamed: D702.2 (A), R702.2
Vmot: C701.1, C703.1, C704.1, C705.1, C707.1, JP701.1 (A); also elsewhere on the board

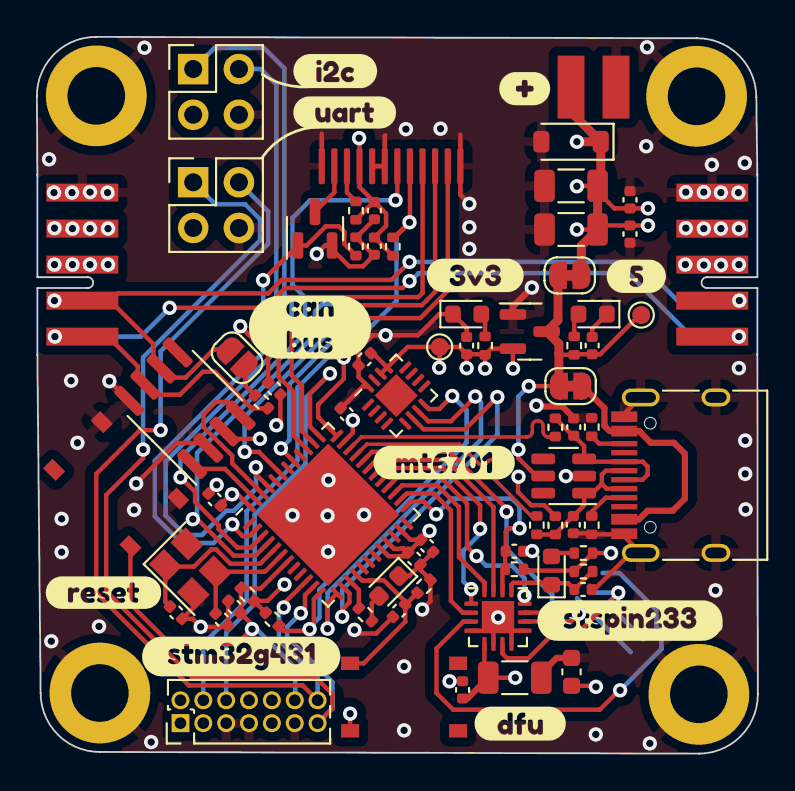
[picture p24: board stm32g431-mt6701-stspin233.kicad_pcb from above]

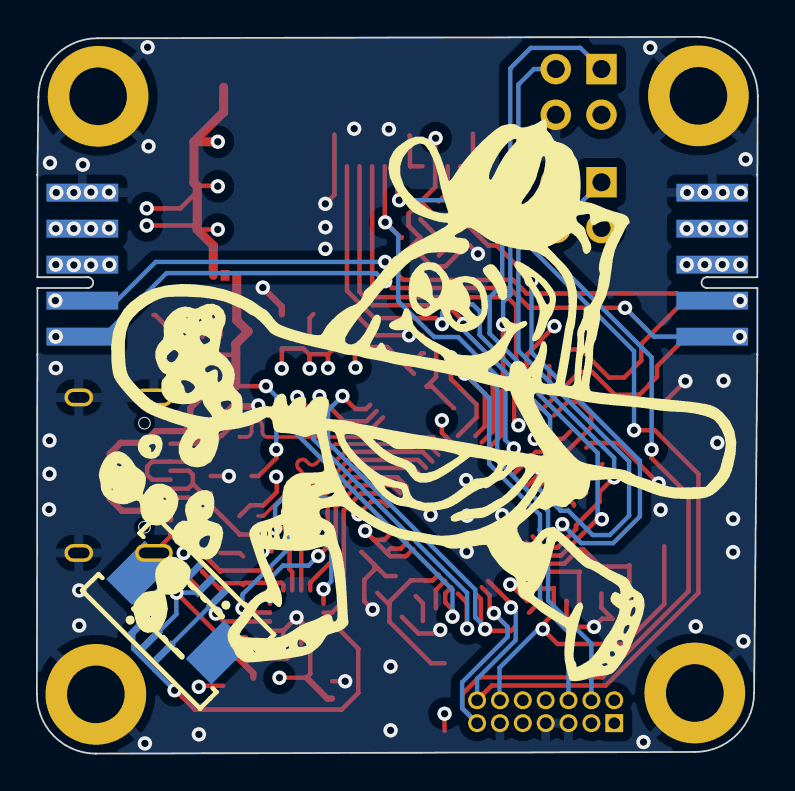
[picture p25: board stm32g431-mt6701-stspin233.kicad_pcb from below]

Board: 4 copper layers, 40.1 x 39.8 mm, 89 parts (5 on the bottom side), 53 nets.

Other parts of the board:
R206, R207: 22R; R_0402_1005Metric
kibuzzard-649CD3B4: G***; kibuzzard-649CD3B4
kibuzzard-649CD3ED: G***; kibuzzard-649CD3ED
kibuzzard-649CD42A: G***; kibuzzard-649CD42A
kibuzzard-649CD53A: G***; kibuzzard-649CD53A
kibuzzard-649CD397: G***; kibuzzard-649CD397
kibuzzard-649CD402: G***; kibuzzard-649CD402
kibuzzard-649CD439: G***; kibuzzard-649CD439
kibuzzard-649CD577: G***; kibuzzard-649CD577
kibuzzard-649D001F: G***; kibuzzard-649D001F
kibuzzard-649D0025: G***; kibuzzard-649D0025
kibuzzard-649DBE26: G***; kibuzzard-649DBE26
kibuzzard-649DBEEB: G***; kibuzzard-649DBEEB

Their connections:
/mcu/USBD_M: R206.1; also elsewhere on the board
/mcu/USBD_P: R207.2; also elsewhere on the board
/mcu/USB_M: R206.2; also elsewhere on the board
/mcu/USB_P: R207.1; also elsewhere on the board

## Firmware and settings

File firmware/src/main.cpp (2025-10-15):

// Copyright 2024 matei jordache <mateijordache@live.com>
#include <Arduino.h>
#include <SPI.h>
#include <SimpleFOC.h>
#include <SimpleFOCDrivers.h>

#include "./aioli-board.h"
#include "./drv_reset.h"
#include "encoders/mt6701/MagneticSensorMT6701SSI.h"

// Motor specific parameters.
#define POLEPAIRS 4
#define RPHASE 1.4
#define MOTORKV 1000

uint8_t useDFU = 0;
uint8_t pendingFrame = 0;
uint8_t sfocCmdStr;

// simpleFOC constructors
BLDCDriver3PWM driver = BLDCDriver3PWM(U_PWM, V_PWM, W_PWM, U_EN, V_EN, W_EN);
BLDCMotor motor = BLDCMotor(POLEPAIRS, RPHASE, MOTORKV);
MagneticSensorMT6701SSI enc = MagneticSensorMT6701SSI(ENC_CS);
Commander commander = Commander(SerialUSB);

uint8_t configureFOC(void);
uint8_t configureDFU(void);
extern uint8_t configureCAN(void);

void doMotor(char *cmd) { commander.motor(&motor, cmd); }

void setup() {
  pinMode(AIOLI_LED, OUTPUT);
  pinMode(AIOLI_BUTTON, INPUT);

  SerialUSB.begin();

  Serial.println(configureFOC() == 1 ? "SFOC successfully init."
                                     : "SFOC failed to init.");
  Serial.println(configureCAN() == 1 ? "CAN successfully init."
                                     : "CAN failed to init.");
  Serial.println(configureDFU() == 1 ? "DFU successfully init."
                                     : "DFU failed to init.");
}

void loop() {
  motor.loopFOC();
  motor.move();
  commander.run();

  // if(pendingFrame){
  //   commander.run((char*)sfocCmdStr);
  //   pendingFrame = 0;
  // }
  // else{
  //   commander.run();
  // }

#ifdef HAS_MONITOR
  motor.monitor();
#endif
}

uint8_t configureFOC() {
  commander.add('M', doMotor, "motor");
  commander.verbose = VerboseMode::machine_readable;

#ifdef SIMPLEFOC_STM_DEBUG
  SimpleFOCDebug::enable(&Serial);
#endif

  // Encoder initialization.
  // Encoder on SPI1
  enc.init();

  // Driver initialization.
  driver.pwm_frequency = 32000;
  driver.voltage_power_supply = 5;
  driver.voltage_limit = 5;
  driver.init();

  // Motor PID parameters.
  motor.PID_velocity.P = 0.2;
  motor.PID_velocity.I = 3;
  motor.PID_velocity.D = 0.002;
  motor.PID_velocity.output_ramp = 100;
  motor.LPF_velocity.Tf = 0.5;
  motor.LPF_angle.Tf = 0;  // try to avoid

  // Motor initialization.
  motor.voltage_sensor_align = 2;
  motor.current_limit = 0.5;
  motor.velocity_limit = 20;
  motor.controller = MotionControlType::velocity;
  motor.foc_modulation = FOCModulationType::SinePWM;

// Monitor initialization
#ifdef HAS_MONITOR
  motor.useMonitoring(Serial);
  motor.monitor_start_char = 'M';
  motor.monitor_end_char = 'M';
  motor.monitor_downsample = 250;
#endif

  motor.linkSensor(&enc);
  motor.linkDriver(&driver);
  motor.init();

  motor.target = 20;

  return motor.initFOC();
}

uint8_t configureCAN() { return 0; }

uint8_t configureDFU() { return 1; }

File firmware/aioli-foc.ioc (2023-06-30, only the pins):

Mcu.UserName=STM32G431CBUx
PA10.Signal=S_TIM1_CH3
PA11.Signal=USB_DM
PA12.Signal=USB_DP
PA13.Signal=SYS_JTMS-SWDIO
PA14.Signal=SYS_JTCK-SWCLK
PA15.Signal=I2C1_SCL
PA2.Signal=USART2_TX
PA3.Signal=USART2_RX
PA5.Signal=SPI1_SCK
PA6.Signal=SPI1_MISO
PA8.Signal=S_TIM1_CH1
PA9.Signal=S_TIM1_CH2
PB13.Signal=TIM1_CH1N
PB14.Signal=TIM1_CH2N
PB15.Signal=TIM1_CH3N
PB3.GPIO_Label=SPI3_CS
PB3.Signal=GPIO_Output
PB4.Signal=UCPD1_CC2
PB6.Signal=UCPD1_CC1
PB7.Signal=I2C1_SDA
PB8-BOOT0.Signal=FDCAN1_RX
PB9.Signal=FDCAN1_TX
PC13.Signal=TIM8_CH4N
PC14-OSC32_IN.GPIO_Label=TFT_DC
PC14-OSC32_IN.Signal=GPIO_Output
PC15-OSC32_OUT.GPIO_Label=TFT_RESET
PC15-OSC32_OUT.Signal=GPIO_Output
PF0-OSC_IN.Signal=RCC_OSC_IN
PF1-OSC_OUT.Signal=RCC_OSC_OUT

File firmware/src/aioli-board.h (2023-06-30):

#pragma once

// MOTOR DRIVER
#define U_PWM       PA8
#define U_EN        PB13
#define V_PWM       PA9
#define V_EN        PB14
#define W_PWM       PA10
#define W_EN        PB15

// MOTOR ENCODER (SPI1)
#define ENC_CIPO    PA6
#define ENC_SCK     PA5
#define ENC_CS      PA4

// CANBUS
#define CAN_TX      PB9
#define CAN_RX      PB8

// GC9AO1 TFT DISPLAY (SPI3)
#define TFT_COPI    PB5    
#define TFT_SCK     PC10
#define TFT_CS      PB3
#define TFT_DC      PC14
#define TFT_BL      PC13 // PWM TIM8CH4N

// GENERAL SPI (SPI3)
#define SPI3_CS     PB11 

// GENERAL UART
#define UART2_TX    PA2
#define UART2_RX    PA3

// GENERAL I2C
#define I2C1_SDA    PB7
#define I2C1_SCL    PA15

//MISC
#define USER_LED    PA7
#define DFU_PIN     PC4

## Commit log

2023-06-22 work on layout
    [display.kicad_sch, driver.kicad_sch, encoder.kicad_sch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]
2023-06-29 finalize fab files
    [JLC-BOM.csv, display.kicad_sch, stm32g431-mt6701-stspin233.csv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]
2023-06-29 fix gitignore
    [JLC-BOM.csv, stm32g431-mt6701-stspin233.csv, stm32g431-mt6701-stspin233.kicad_pcb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]
2023-06-30 update schematic
    [stm32g431-mt6701-stspin233.kicad_sch]
2023-06-30 fix board dir
2023-07-01 start on adding CANBUS
2023-07-03 update schematic (Vref+ tie to Vdd) and go through ERC check
    [encoder.kicad_sch, mcu.kicad_sch, psu.kicad_sch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]
2023-07-07 Update with real photos
    [stm32g431-mt6701-stspin233.kicad_pcb]
2023-07-08 Fix swapped USB pins
    [stm32g431-mt6701-stspin233.kicad_pcb, stm32g431-mt6701-stspin233.kicad_sch, usb.kicad_sch]
2023-07-11 update schematic to remove debounce cap
    [display.kicad_sch, mcu.kicad_sch, psu.kicad_sch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]
2023-07-12 Add cpl, bom, fix soldermask on edge conn
    [JLC-BOM.csv, stm32g431-mt6701-stspin233.kicad_pcb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]
2023-07-14 Add mechanical files
    [aiolifoc-backplane.FCStd, aiolifoc-backplane.stl, aiolifoc.FCStd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]
2023-07-15 Add assembly files
    [stm32g431-mt6701-stspin233-B_Cu.gbr, stm32g431-mt6701-stspin233-B_Mask.gbr, stm32g431-mt6701-stspin233-B_Paste.gbr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]
2024-05-22 Fix up imports, fix typo in BOM, start readme
    [JLC-BOM.csv]
2024-05-23 Add pre-commit and linters/formatters
    [defaults.cfg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]
2024-05-23 Add a bunch of linting
    [CPPLINT.cfg]
2024-05-23 Nuke accidentally added file
    [defaults.cfg]
